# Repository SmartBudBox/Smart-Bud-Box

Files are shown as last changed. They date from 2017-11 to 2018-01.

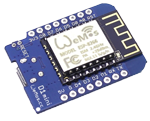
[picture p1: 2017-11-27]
Setup Tool/SBB Tool Source Code/Resources/WeMosV1.png

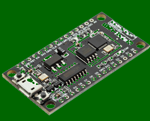
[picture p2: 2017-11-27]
Setup Tool/SBB Tool Source Code/Resources/WemosV2_activ.png

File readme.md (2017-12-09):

# Smart-Bud-Box
A small full automatic DIY Growbox with Web Interface for everyone.

# Install
Read the Manuals at /instrcutions/ for build the box and set up the Interface. We also got a little Growbook for the first steps

## Todo
- languages files for multilang
- ((write a growbook)) and put it to interface
- Addons like: libra, temp/humi for othside

## Wanna help?
You can help me by translate the language files (comming soon) into your langauge or make a new web design =)

## Short Video from the Interace with Planer
https://streamable.com/1owan

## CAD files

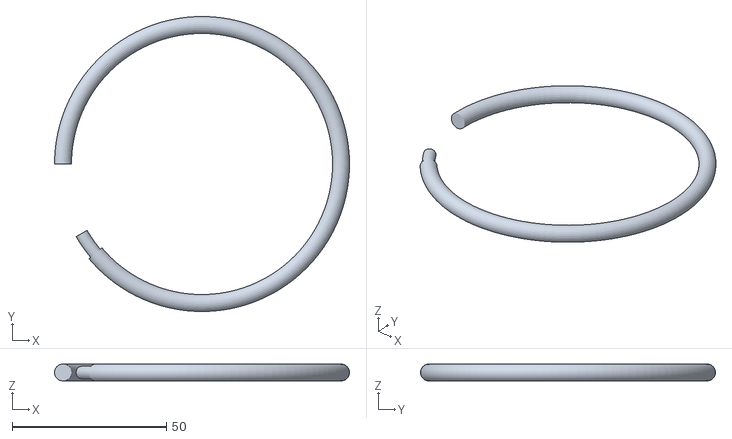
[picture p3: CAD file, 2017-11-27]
build_the_box/3d_printable_parts/water_ring_4mm_big.stl
95.5 x 95.5 x 5.48

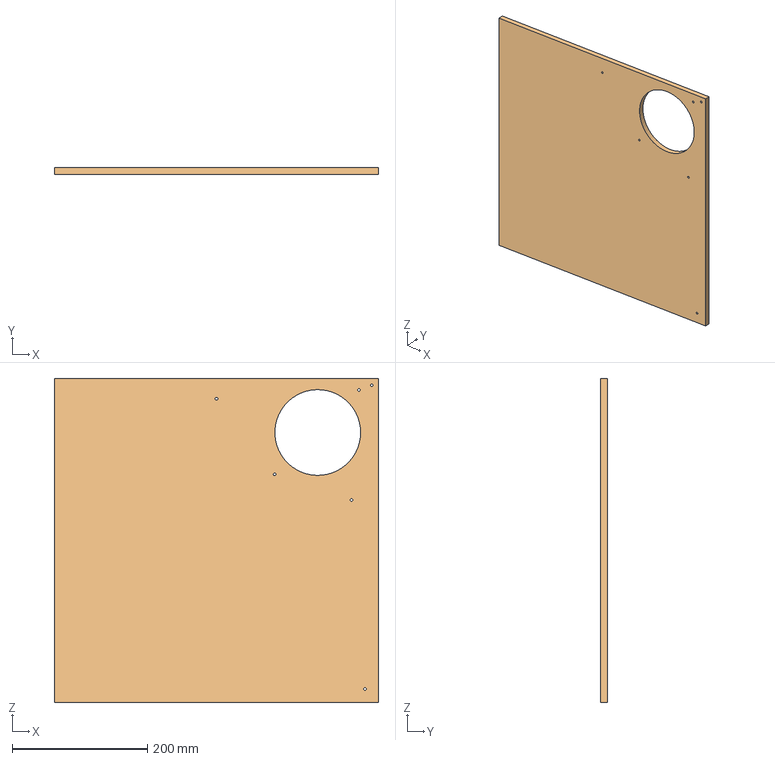
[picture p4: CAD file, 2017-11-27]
build_the_box/FreeCAD/FreeCAD_sbb.FCStd
480.0 x 10.0 x 480.0 mm

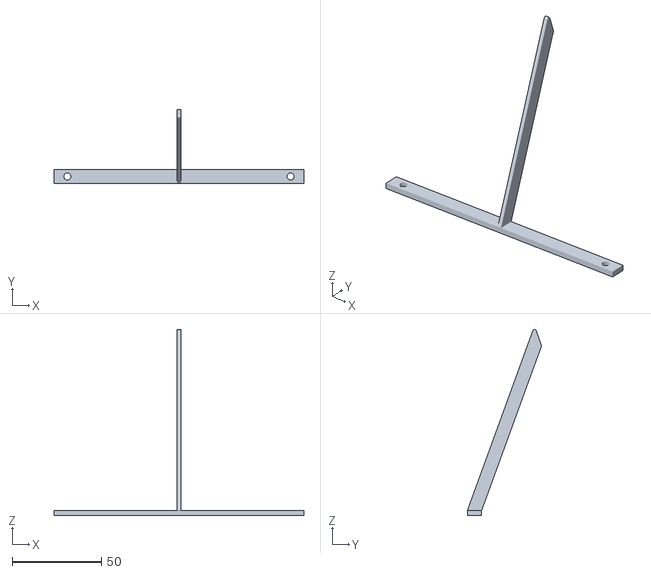
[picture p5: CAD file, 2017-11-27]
build_the_box/3d_printable_parts/140mm_fan_stand.stl
140.0 x 41.5 x 104.4

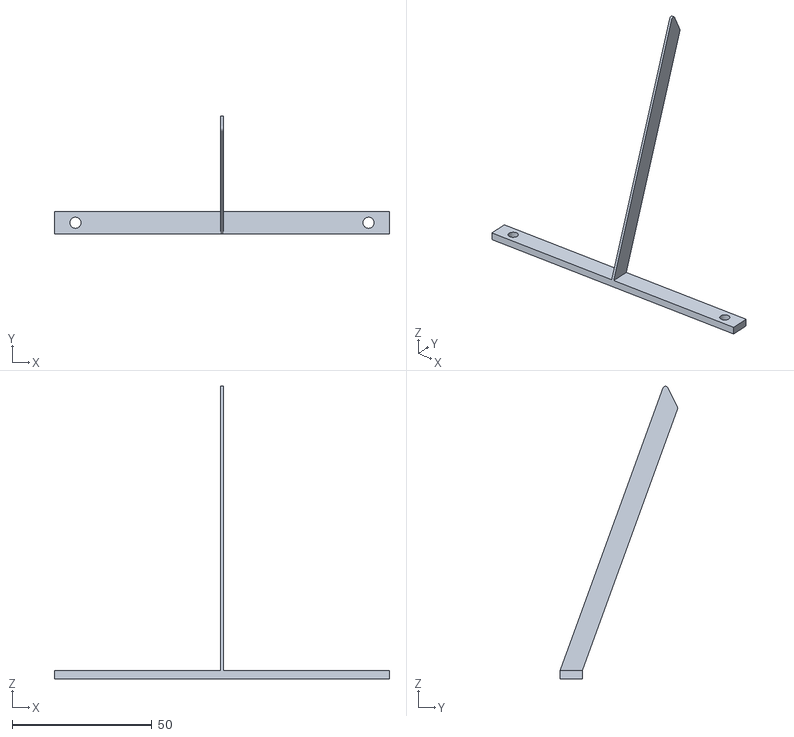
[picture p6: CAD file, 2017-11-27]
build_the_box/3d_printable_parts/120mm_fan_stand.stl
120.0 x 42.2 x 104.8

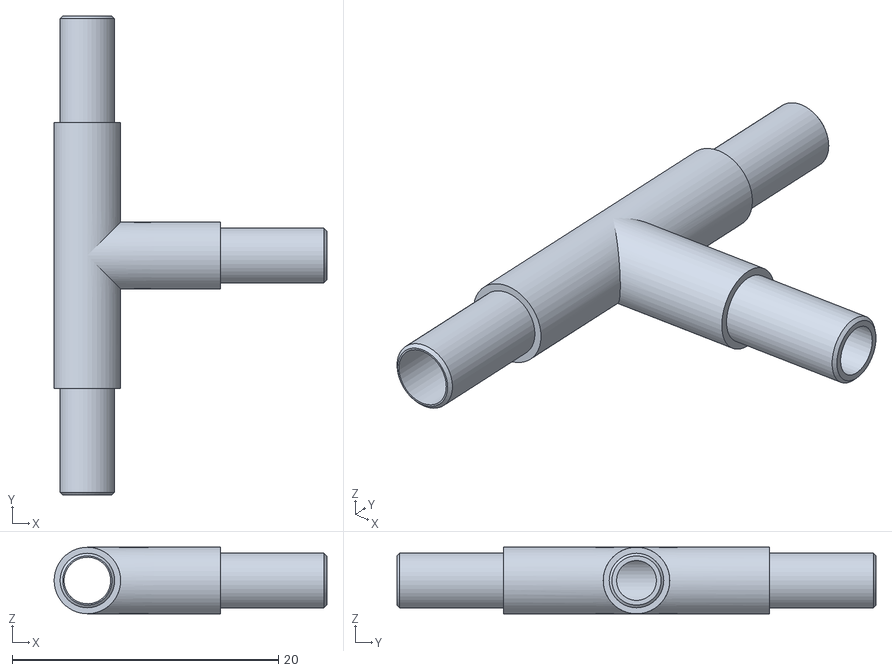
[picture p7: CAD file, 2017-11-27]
build_the_box/3d_printable_parts/t-hose.connector.stl
20.5 x 36.0 x 5.00

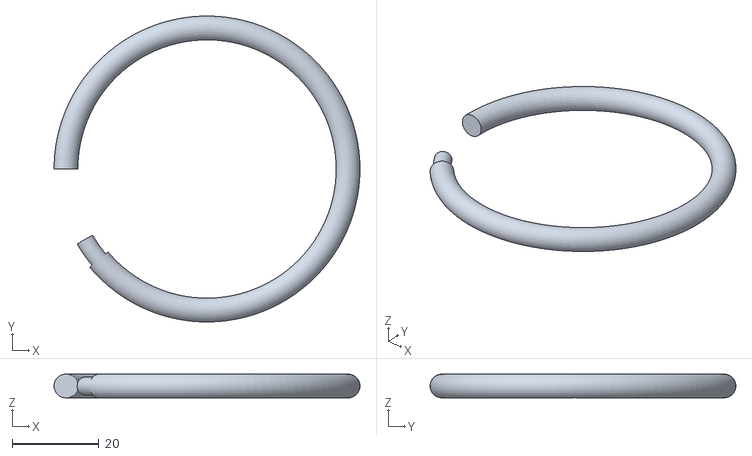
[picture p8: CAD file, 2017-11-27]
build_the_box/3d_printable_parts/water_ring_4mm_small.stl
70.5 x 70.5 x 5.48

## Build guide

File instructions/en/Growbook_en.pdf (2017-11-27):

# Preparation & Equipment

Selecting seeds
Buy feminised seeds from plants that don't get too big, indicas have an advantage. I can recommend www.Samenwahl.com as a source.

If you don't know what you want to plant, you can look for a certain variety in the seed database and sort by effect and many more: http://seedfinder.eu

Fertilizer | & | PH-Down
As a fertilizer I recommend you to add a mineral All-In-One fertilizer to the water: Hy-Pro Terra 500ml. Hy-Pro also has a liquid PH-down, you need a PH-down to lower the PH of your tap water (is 7) because the plant can only process the nutrients properly at 5.5-6PH. Rainwater would also be suitable as the PH value is lower from the house.

PH meter
Buy a PH meter to check your water for 10€ and you will get a good value (yellow meter).
Growing | and | potting | soil
You need two kinds of soils, one is a cultivating/herbal soil which is not so heavily fertilized for the beginning and the other one is potting soil for the further development. I recommend Compo Sana quality soil from the hardware store, you have a good price/performance ratio.

Jars
In order to preserve your harvest later on, you will need preserving jars, which are well sealed. I recommend 1-2 pieces with 1 litre capacity.
Flowerpot | with | saucer
Here, cheap plant pots with coasters from the DIY store are enough. It is important that the pot has holes at the bottom so that the water can get out. After all, water is always poured down to the bottom so that the fertiliser does not deposit. Get yourself three different sizes, a very small one for the cultivation (large diameter of your fist), a medium one (two fists diameter) and a big one (three fists diameter).
Ikea | 365+ | Reservoir | 2.3 | litres
We need the container as a water tank, if you have something similar at home and it fits into the box you can also take it. The advantage of the container is that you can make a mark at 2 liters. Then you only have to add water up to the mark Hy-Pro Terra (10ml) and adjust the pH value.

# Germination process

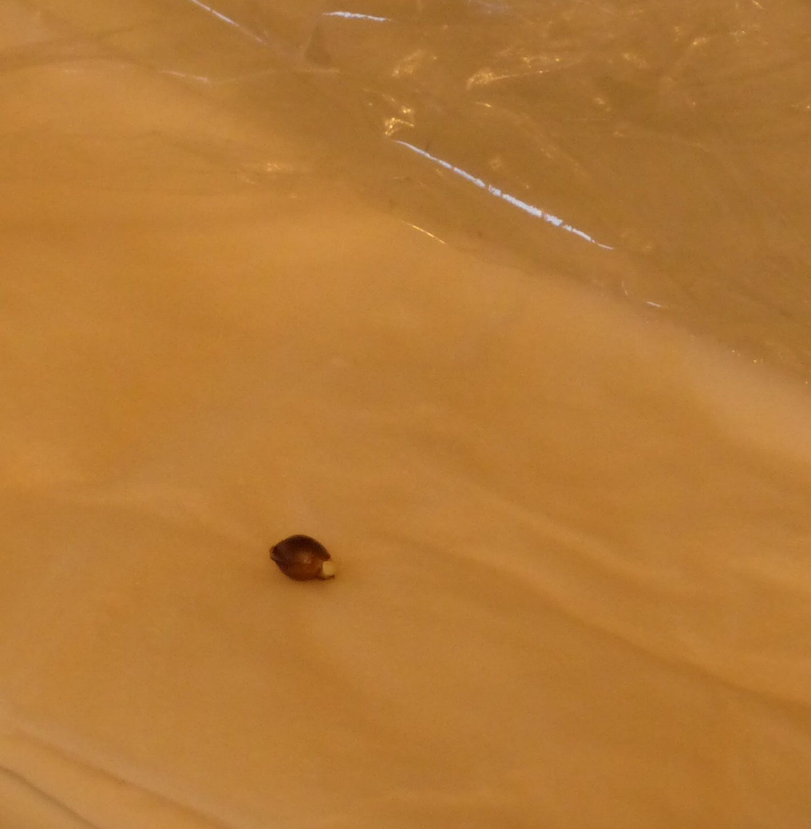
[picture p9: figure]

Duration: 2-6 days

For germination you need two small plates, two handkerchiefs, the seed and cling film. Now take a plate and put a handkerchief on it, moisten it well in front of it and then put the seed on it. The second handkerchief is also well moistened and put over it and a little bit pressed on. Then cover the whole thing with cling film so that the moisture cannot escape. Now you take the second plate and put it on top of it so there's no light coming in. Give the seed three days to germinate, then the rind opens and a small, fine root emerges.

# Pot seeds

If your seeds are germinated, you can take a small flower bowl and fill it with cultivated soil, fill the bowl with about 75 %. Then take the germinated seed with a pair of tweezers and place it in the middle with the root pointing downwards, then add one to two centimetres of soil and add it to the ground and water it well with normal water, preferably with a spoon or directly with the watering system.

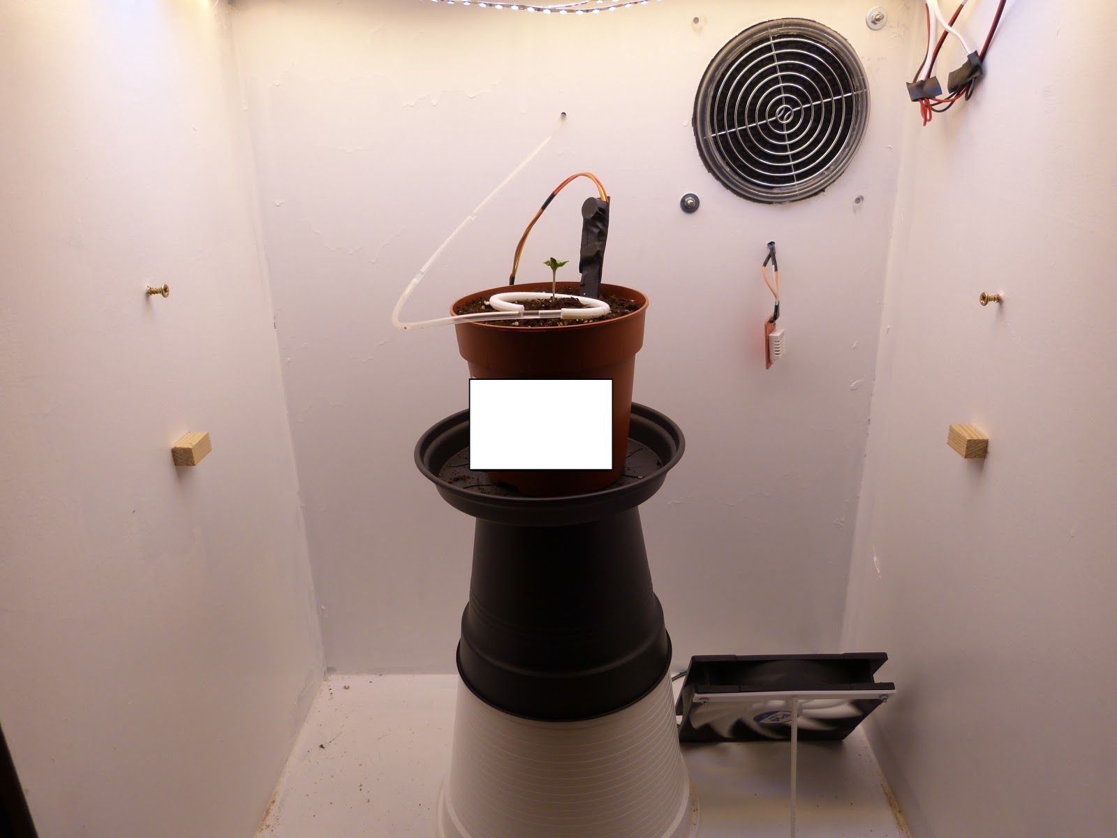
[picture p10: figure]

For the casting system, please proceed slowly,
e. g. with a casting time of 1000 milliseconds
and a waiting time of 200 seconds. The repetitions can be done at the beginning in two places depending on how big your pot is, your soil moisture reaches a value of about 500 the soil is wet and from 360-400 about the soil is dry again and you have to water again. You can see this best if the curve of the earth's moisture does not go down anymore but only
sideways.

Put the pot in the middle of the box, because the white lights are important for the vegetation phase, you can also put them underneath so that the plant is closer to the light. If you have installed a switch, you can turn off the warm white lights. With the lighting I advise you to have 20 hours of lighting and 4 hours rest I turn off my lights at 12 o' clock on and at 8 o' clock in the morning. You can now set the counter to the flower by clicking on it.

Now the seed can unfold and your plant can grow, make sure you don't water too much and stick to the sensor. Sometimes less is more.

# Growing season

Duration: approx. 2 weeks

The first vegetation phase is about 2 weeks, which means that the plant grows up. The best values are humidity at least 40% and the temperature at least 22 degrees Celsius. If you get too dry air, take a glass or bowl with a cloth in it and fill it with water, the cloth should stick out and put on the water.

At the beginning a plant grows quite fast and after two or three days you can fill up a little soil until the pot is completely filled.

Also, raise the pot a little higher at the beginning so that the plant gets enough light. If you take fruit flies, take a small glass of vodka glass, fill it with 50% water, 50% wine vinegar and a drop of water, then you have a good flytrap.

# Repot the plant

Duration: 7 days

Now look out of the pot and the first pair of leaves has formed (not the germination leaves) it is time to plant in the medium-sized pot and change the soil to the potting soil or add fertiliser via the water. If the soil is dry when repotting, it will be easier.

Take the medium-sized pot and fill it up to 30 % with the potting soil, then take the old pot and bend it a little bit on the sides so that you can get the plant out. Shake the soil around the plant as much as you can, but the plant does not exist. Now place the plant in your new pot and fill it with potting soil.

If the potting action is successful, you can water again and let your plant grow.

Don't be surprised if after potting the time takes longer until the soil would be dry (up to 7 days) this is normal as the roots dig in again and stretch out before the plant gets really thirsty again.

If the leaves should sink after repotting, it is quite normal that the roots need a little bit of time to cope with it.

# Topping

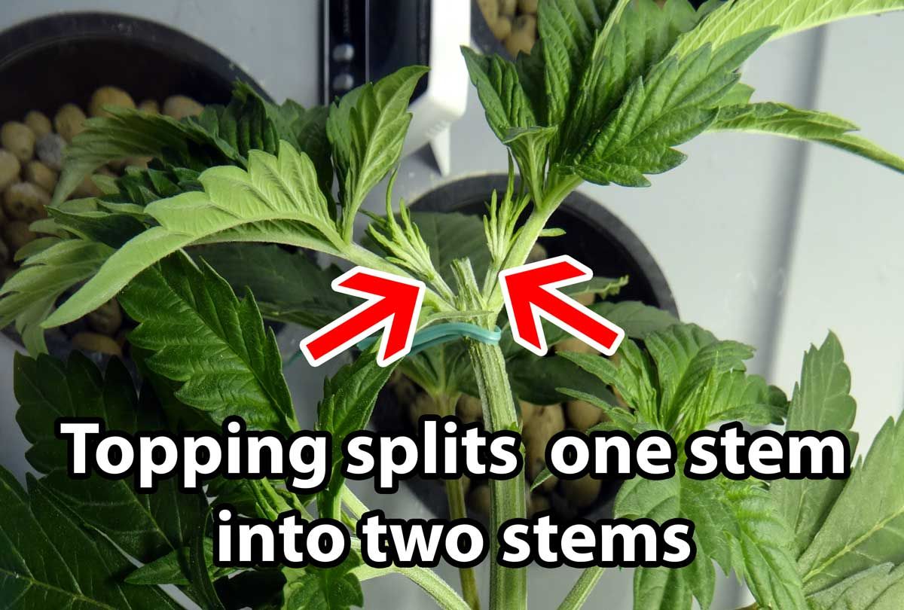
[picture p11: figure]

Duration: 3 days

If your plant already has the third pair of leaves and it still grows a little bit out in the middle, you can cut your plant there with a disinfected knife, scissors or something like that. Thus it does not grow up into the height anymore but forms several main drives which we can pass later on under the lattice. That increases your request considerably.

# Repot plant 2 & vegi 2

Duration: 2-5 weeks

Give your plant two to three days to recover after topping. Afterwards you can plant the pot in the middle pot on the big pot with potting soil.

Just follow the same procedure as for the first repot action. If your plant is too small from the height or grows rather bushy, you can repot it in such a way that just the root is planted in the ground and the stem sticks out more into the height. If not, repot the pot normally.

When your plant reaches the height of the lattice, place the lattice on top and let the stems grow through. As soon as the stem is through a grid, gently pull it down into the next grid hole. This way you can spread your main shoots in length.

# Blooming phase

Duration: 50-70 days

If the plant has grown well under the lattice, you can start flowering and the flowering can be initiated before. Depending on how much you want in Erne. Note also that in the flowering phase your plant grows again properly, so 50% of what it already is. It can be pulled through the grids, depending on how much space is available.

To start flowering with normal seeds (no automatics) you just have to change the lighting cycle to 12 hours of light 12 hours dark. The cold white light can now be switched off because the plant needs more warm white. It wouldn't matter if you added lighting, but it costs more electricity and the temperature in the box is higher.

The plant slowly gets hairs from which new shoots are formed and they should have a free path to the light, work a little bit with the lattice and pull down larger leaves. Around the flowers you will notice small white dots, the resin glands that become active and at the same time your plant will become thirsty. If you have poured in the vegi every 3-7 days it can happen that you now pour every 2 days.

About 2 weeks before harvesting you should leave off the fertilizer so that the plant can rinse all the minerals and you don't scratch later. Towards the end the leaves turn yellow, which is normal in autumn and the trees outside are no longer green.

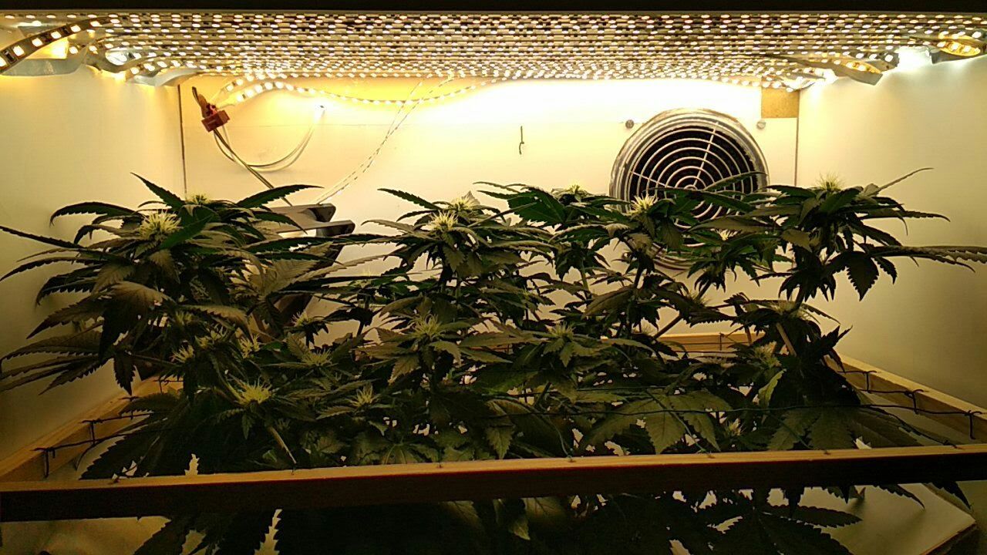
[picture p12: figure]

# Harvesting & Drying

Duration: 2 weeks

The flowering period lasts for about 2 months, 50-70 days depending on the variety. The information from the manufacturer is usually always very positive. You can also influence the effect of the harvest. Look at this graphic. Best you use a microscope eg for the PC, which are quite cheap to have.

Look at this when you harvest the soil is dry to get some moisture out of it. Before harvesting, it is advisable to turn off the light for 24 hours to send the plant to sleep.

When the day has come, you will
get some garden wire/string,
disposable gloves and a good pair
of scissors. Make sure that you stay undisturbed (nights) and that you have closed the room, the smell will be extreme. Cut off the sun sails (large blades) on the main propulsion. Then cut off the main drive at the bottom and thread it out of the grid, the more you do away from it, the better it goes.

If you have the main shoots removed, then cut the leaves off around the blossoms, if the small leaves remain on the blossom it is half as bad, there is enough resin on it that it is worthwhile to use them with.

Clears out the box and stretches the string across the Growroom on
the screws to the right and left of
the wall. Hang the shoots like on a

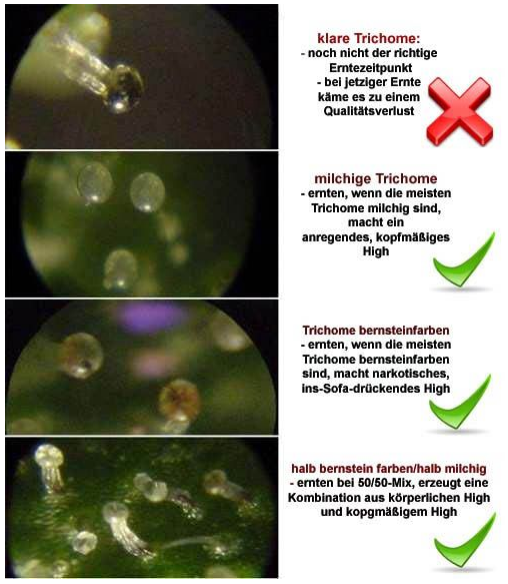
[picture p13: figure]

clothesline. Turns off the light of the box by pressing the green "Light" button.

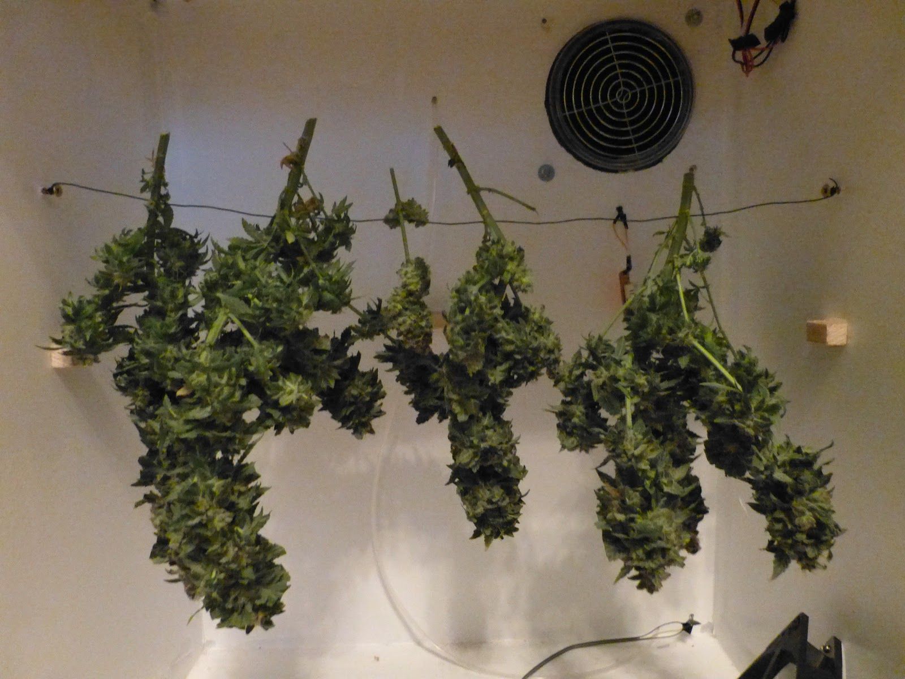
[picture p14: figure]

Now the 2 weeks are best left in the dark at 50% humidity until the main shoots break when bending. Then it's dry enough. Now you can cut the flowers from the main shoots or break them off as you like.

# Curing

Duration: min. 2 weeks

If you have the flowers then put them into the preserving jar, it is best if the jars are only half full. In the first 1-2 weeks you open the preserving jars daily so that the humidity can get out and it doesn't mildew.

After that you're finished, the curing process can be optimized and you can do up to two years, google it, then you can really refine the stuff and experience tastes you didn't know before.

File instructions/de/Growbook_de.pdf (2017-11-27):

# Vorbereitung & Equipment

Samen aussuchen
Kauft euch feminisierte Samen von Pflanzen die nicht all zu groß werden, indicas sind da im Vorteil. Als Quelle kann ich www.Samenwahl.com empfehlen.

Wenn ihr nicht wisst was ihr anpflanzen wollt könnt ihr bei der Samendatenbank erst einmal nach einer gewissen Sorte Ausschau halten und dabei nach Wirkung und vielen weiteren sortieren: http://seedfinder.eu

Dünger | & | PH-Down
Als Dünger empfehle ich euch einen mineralischen All-In-One Dünger den ihr mit in das Wasser gebt: Hy-Pro Terra 500ml. Von Hy-Pro gibt es auch einen flüssigen PH-Down, einen PH-Down braucht ihr um den PH Wert eures Leitungswassers zu senken (liegt bei 7), denn die Pflanze kann nur bei 5,5-6PH die Nährstoffe sauber verarbeiten. Regenwasser würde sich auch eignen da dort der PH Wert von haus aus niedriger ist.

PH Messgerät
Kauft euch für 10€ ein PH Messgerät mit dem ihr euer Wasser überprüfen könnt, sonei günstiges reicht (gelbes Gerät).
Anzucht | und | Blumenerde
Ihr braucht zwei Arten von Erden, einmal eine Anzucht / Kräutererde die nicht so stark gedüngt ist für den Anfang und danach Blumenerde für den weiteren Verlauf. Ich empfehle Compo Sana Qualitätserde aus dem Baumarkt, da habt ihr ein gutes Preis/Leistungsverhältnis.

Einmachgläser
Um später eure Ernte auf zu bewahren braucht ihr Einmachgläser, die sind gut dicht. Ich empfehle 1-2 Stück mit 1 Liter Rauminhalt.
Blumentopf | mit | Untersetzer
Hier reichen so günstige Pflanzenbecher mit Untersetzer aus dem Baumarkt. Wichtig ist dass der Topf unten Löcher hat das dort das Wasser raus kann. Denn gegossen wird immer so viel bis unten Wasser raus kommt damit sich der Dünger nicht ablagern kann. Besorgt euch drei verschiedene Größen, ein ganz kleinen für die Anzucht (Faustgroßer Durchmesser), einen mittleren (zwei Fäuste Durchmesser) und einen großen (drei Fäuste Durchmesser).
Ikea | 365+ | Vorratsbehälter | 2,3 | Liter
Den Behälter benötigen wir als Wassertank, wenn ihr so was ähnliches daheim habt und es in die Box passt könnt ihr das auch nehmen. Der Vorteil bei dem Behälter ist dass man sich bei 2 Liter eine Markierung machen kann. Dann muss man nur bis zur Markierung Wasser rein, eine Verschlusskappe Hy-Pro Terra (10ml) rein und den PH Wert anpassen.

# Keimung

Dauer: 2-6 Tage

Für die Keimung braucht ihr zwei kleine Teller zwei Taschentücher, den Samen und Frischhaltefolie. Nehmt nun ein Teller und legt dort ein Taschentuch drauf, macht es davor gut feucht und legt danach den Samen darauf. Das zweite Taschentuch wird ebenfalls gut feucht gemacht und drüber gelegt und ein bisschen angedrückt. Danach das Ganze mit Frischhaltefolie überziehen damit die Feuchtigkeit
nicht entweichen kann. Jetzt nehmt ihr den zweiten
Tellern und leg den oben drauf damit kein Licht
reinkommt. Gib dem Samen ruhig drei Tage Zeit bis dieser keimen kann, dann öffnet sich die Schale und es dringt eine kleine feine Wurzel heraus.

# Samen eintopfen


Ist eurer Samen gekeimt könnt ihr ein kleine Blumenschale nehmen und diese mit Anzuchterde füllen, füllt die Schale mit ca 75 %. Danach nehmt ihr am besten mit einer Pinzette den gekeimten Samen und legt ihn in die Mitte rein mit der Wurzel nach unten, danach noch ein bis zwei cm Erde drauf und das ganze erstmal gut angießen mit normalen Wasser, am besten mit einem Löffel oder direkt mit dem Gießsystem.

Bei dem die Gießsystem geht bitte langsam vor z.b. mit einer Gießzeit von 1000 Millisekunden und einer Wartezeit von 200 Sekunden. Die Wiederholungen könnt ihr am Anfang auf zwei Stellen je nachdem wie
groß euer Topf ist, erreicht eure Erdfeuchte
ein Wert von ca. 500 ist die Erde nass und
ab 360-400 ungefähr ist die Erde wieder trocken und ihr müsst wieder gießen. Das erkennt ihr am besten daran wenn die Kurve


der Erdfeuchte nicht mehr runter geht sondern nur noch seitwärts.

Stellt den Topf am besten in die Mitte der Box da dort die weißen Lichter sind die für die Vegetationsphase wichtig sind, ihr könnt auch etwas drunter Stellen damit die Pflanze näher am Licht ist. Falls ihr einen Schalter verbaut habt dann könnt ihr die warmweißen Lichter ausschalten. Bei der Beleuchtung rate ich euch zu 20 Stunden Beleuchtung und 4 Stunden Ruhezeit ich schalte mein Licht um 12 Uhr an und um 8 Uhr morgens aus. Den Zähler könnt ihr nun auf die Blüte stellen mit einem Klick darauf.

Jetzt kann der Samen sich entfalten und eure Pflanze kann wachsen, achtet darauf dass ihr nicht zu viel gießen tut und haltet euch an den Sensor. Manchmal ist weniger mehr.

# Vegetationsphase

Dauer: ca. 2 Wochen

Die erste Vegetationsphase geht ca 2 Wochen, sie die dazu dass die Pflanze erstmal groß wird. Die besten Werte dazu sind Luftfeuchtigkeit mindestens 40% und die Temperatur mindestens auf 22 Grad. Falls ihr eine zu trockene Luft bekommt ein Glas oder eine Schale mit einem Tuch darin nehmen und mit Wasser befüllen, das Tuch sollte herausragen und das Wasser anziehen.

Am Anfang wächst eine Pflanze ziemlich schnell und ihr könnt nach zwei oder drei Tagen schon ein bisschen Erde nachschütten so lange bis der Topf komplett gefüllt ist.

Stellt den Topf auch ein wenig höher am Anfang damit die Pflanze genug Licht bekommt. Wenn ihr Fruchtfliegen war nimmt, nehmt ein kleines Glas (Wodkaglas), füllt es 50% mit Wasser, 50% mit Weinessig und einen tropfen Spüli, dann habt ihr eine gute Fliegenfalle.

# Pflanze umtopfen

Dauer: 7 Tage

Schaut eure Pflanze nun gut aus dem Topf und das erste Blattpaar hat sich gebildet (nicht die Keimungsblätter) wird es Zeit in den mittelgroßen Topf um zu pflanzen und die Erde auf die Blumenerde zu wechseln bzw über das Wasser Dünger zuzuführen. Schaut das beim umtopfen die Erde trocken ist, dann geht es einfacher.

Nimm den mittelgroßen Topf und füllt ihn zu 30 % mit der Blumenerde auf, danach nehmt ihr den alten Topf knickt ihn an den Seiten ein wenig ein so dass ihr die Pflanze raus bekommt. Schüttelt um die Pflanze die Erde so gut es geht ab aber besteht nicht die Pflanze. Nun legt ihr die Pflanze in eurer neuen Topf rein und füllt diese mit Blumenerde auf.

Ist die Umtopfaktion geglückt könnt ihr erstmal wieder gießen und eure Pflanze wachsen lassen.

Wundert euch nicht wenn nach dem umtopfen die Zeit länger dauert bis die Erde würde trocken ist (bis zu 7 Tage) das ist normal da die Wurzeln sich erstmal wieder eingraben und ausstrecken bevor die Pflanze wieder richtig durstig wird.

Wenn sich die Blätter senken sollten nach dem Umtopfen ist das ganz normal die Wurzeln brauchen ein bisschen bis sie wieder klar kommen.

# Topping


Dauer: 3 Tage

Hat eure Pflanze schon das dritte Blattpaar und es wächst in der Mitte noch ein wenig raus könnt ihr dort eure Pflanze mit einem desinfizierten Messer, Schere oder sowas in der Art abschneiden. Dadurch wächst sie nicht mehr in die Höhe sondern bildet mehrere Haupttriebe die wir später unterm Gitter hindurch führen können. Das steigert euren Antrag erheblich.

# Pflanze umtopfen 2 & Vegi 2

Dauer: 2-5 Wochen

Gibt eure Pflanze nach dem Topping zwei bis drei Tage Zeit sich zu erholen. Danach könnt ihr von dem mittleren Topf auf den großen Topf umpflanzen wieder mit Blumenerde.

Geht einfach wieder so vor wie bei der ersten umtopf Aktion. Sollte eure Pflanze von der Höhe her zu klein sein oder eher buschig wachsen könnt ihr die so umtopfen dass gerade die Wurzel in die Erde steckt und der Stiel mehr in die Höhe ragt. Anderenfalls ganz normal wieder umtopfen.

Erreicht eure Pflanze die Höhe vom Gitter, dann legt das Gitter drauf und lasst die Stängel durch wachsen. Sobald der Stängel durch ein Gitter ist, zieht ihn vorsichtig runter in das nächste Gitterloch. So könnt ihr eure Haupttriebe schön in die Länge spreizen.

# Blütephase

Dauer: 50-70 Tage

Ist die Pflanze schon schön unterm Gitter gewachsen könnt ihr die Blüte einleiten, die Blüte kann auch schon zuvor eingeleitet werden. Je nach dem wie viel ihr an Erne wollt. Beachtet auch dass in der Blütephase eure Pflanze nochmals ordentlich wächst, so 50% von dem was sie schon ist. Dabei kann sie weiterhin durch die Gitter gezogen werden, je nachdem wieviel Platz noch vorhanden ist.

Um Die Blütephase einzuleiten bei normalen Samen (keine Automatics) müsst ihr einfach den Beleuchtungszyklus ändern auf 12 Stunden Licht 12 Stunden dunkel. Das Kaltweiße Licht kann jetzt abgeschaltet werden, da die Pflanze nun mehr Warmweiss braucht. Zwar würde es nichts ausmachen zusätzlich zu beleuchten, aber das kostet mehr Strom und die Temperatur in der Box ist höher.

Die Pflanze bekommt langsam Härchen aus denen sich neue Triebe bilden und die sollten möglichst freie Bahn haben zum Licht, arbeitet ein bisschen mit dem Gitter und zieht größere Blätter runter. Um die Blüten herum werdet ihr kleine weiße Punkte wahrnehmen, das sind die Harzdrüsen die aktiv werden, gleichzeitig wird eure Pflanze auch durstiger. Habt ihr in der Vegi noch alle 3-7 tage einmal gegossen kann es vorkommen dass ihr jetzt alle 2 Tage gießt.

Ca. 2 Wochen bevor ihr erntet solltet ihr den Dünger weg lassen damit die Pflanze die ganzen Mineralien ausspülen kann und ihr später kein Kratzen habt. Gegen Ende werden die Blätter gelb, das ist normal im Herbst sind die Bäume draußen auch nicht mehr grün.

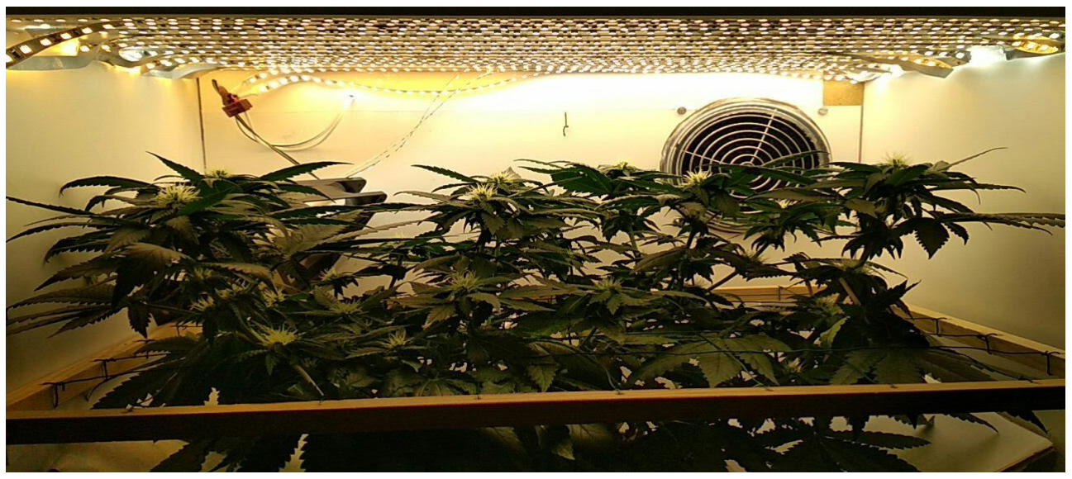
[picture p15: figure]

# Ernte & Trocknung

Dauer: 2 Wochen

Die Blütephase geht ca. 2 Monate lang so 50-70 Tage je nach Sorte. Die Angaben vom Hersteller sind meist immer sehr positiv. Durch die Ernte könnt ihr auch nochmal die Wirkung beeinflussen. Schau dabei auf diese Grafik. Am besten ihr verwendet ein Mikroskop zB für den PC, die sind recht günstig zu haben.

Schaut das wenn ihr Erntet die Erde trocken ist um so schonmal Feuchtigkeit raus zu bekommen. Bevor man erntet sollte man auch 24 Stunden lang das Licht ausschalten um die Pflanze in den Schlaf zu schicken.

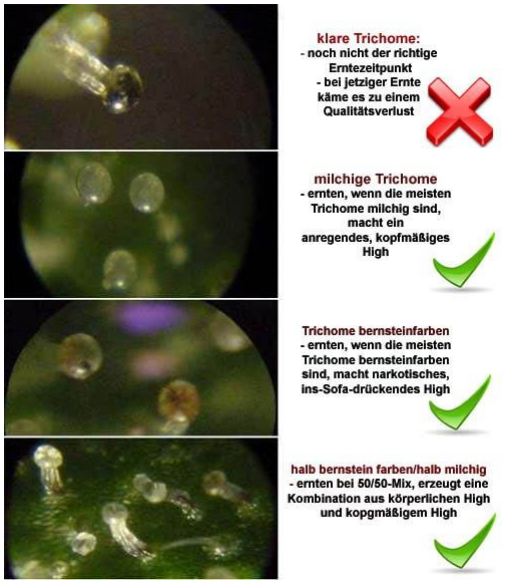
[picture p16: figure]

Ist der Tag gekommen dann legt
euch Gartendraht/schnur,
Einweghandschuhe und eine gute Schere zu. Achtet dass ihr ungestört bleibt (Nachts) und das ihr den Raum geschlossen habt, der Geruch wird extrem. Trennt dann die Sonnensegel (große Blätter) am Haupttrieb ab. Danach den Haupttrieb unten abschneiden und aus dem Gitter fädeln, umso mehr ihr davor weg macht umso besser geht es auch raus.

Habt ihr die Haupttriebe weg, dann schneidet um die Blüten die Blätter noch weg, wenn die kleinen Blätter an der Blüte dran bleiben ist das halb so schlimm, da ist genug Harz dran das es sich lohnt diese mit zu verwerten.

Räumt die Box aus und spannt die Schnur quer durch den Growroom an den Schrauben rechts und links der Wand. Hängt da die
Triebe auf wie auf einer Wäscheleine.
Schaltet das Licht der Box aus, dazu auf
den grünen “Licht” Button drücken.


Jetzt bleiben die 2 Wochen am besten bei 50% Luftfeuchte im dunklem hängen, bis sich die Haupttriebe beim biegen brechen. Dann ist es trocken genug. Jetzt könnt ihr die Blüten von den Haupttrieben abschneiden bzw abbrechen, wie ihr wollt.

# Aushärten

Dauer: min. 2 Wochen

Habt ihr die Blüten dann ab damit in das Einmachglas, am besten ist es wenn die Gläser nur zur Hälfte gefüllt sind. In den ersten 1-2 Wochen öffnet ihr die Einmachgläser täglich damit die Luftfeuchte raus kann und es nicht schimmelt.

Danach ist seit ihr eigentlich schon fertig, das Aushärten kann man noch optimieren und bis zu zwei JAhre betreiben, am besten mal googeln, dann könnt ihr das Zeug richtig veredeln und werdet Geschmäcke erleben die ihr nicht kanntet.

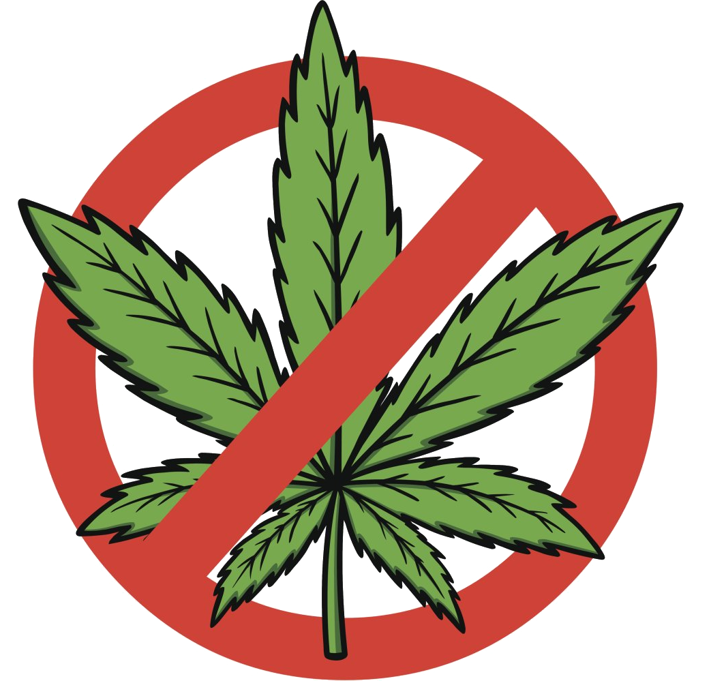
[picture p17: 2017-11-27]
Setup Tool/SBB Tool Source Code/Resources/Close.png

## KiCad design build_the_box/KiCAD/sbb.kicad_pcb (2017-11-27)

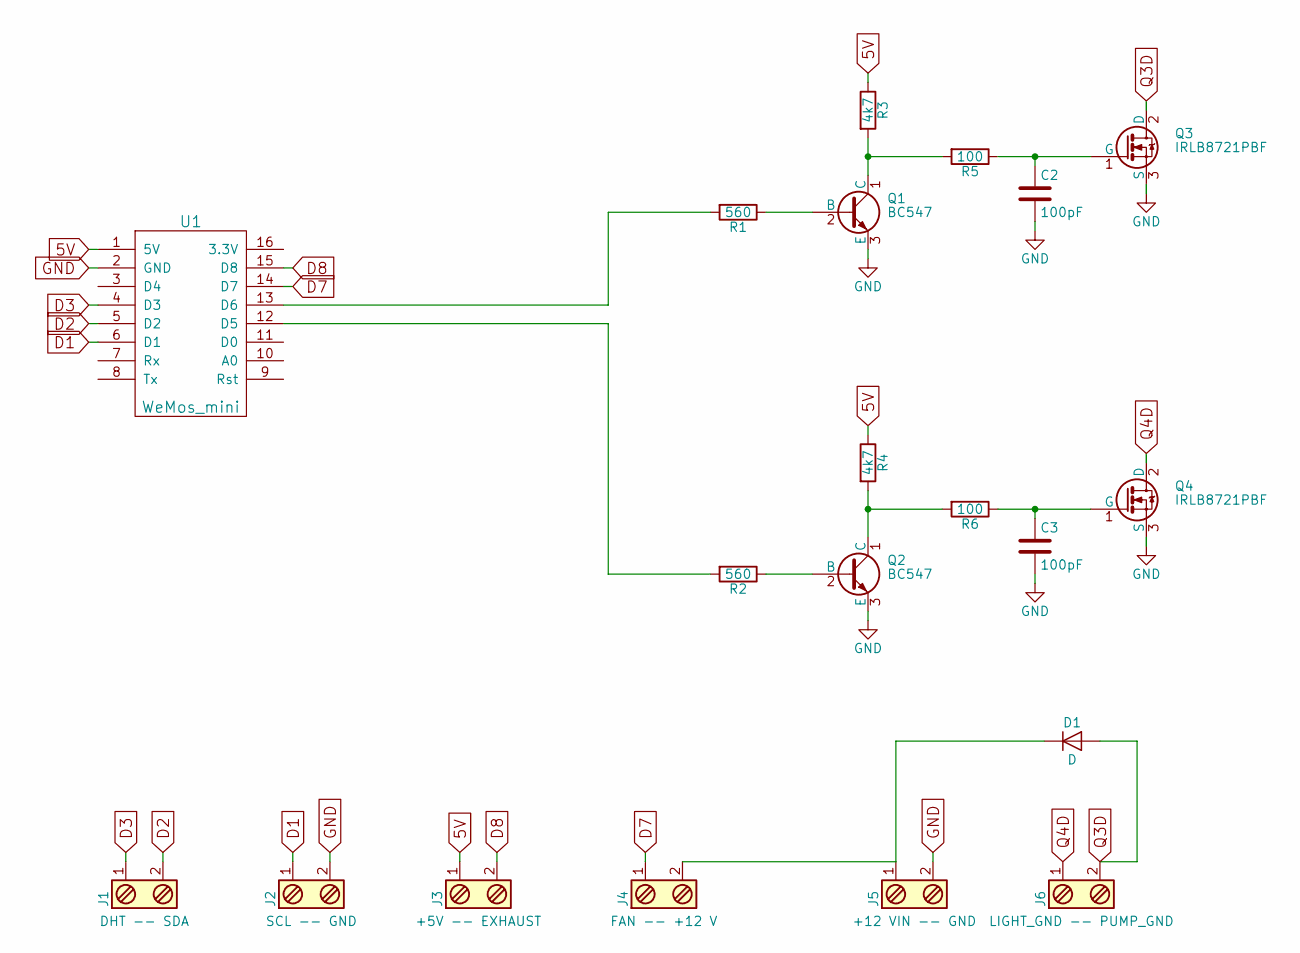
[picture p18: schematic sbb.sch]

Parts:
C2, C3: 100pF; C_Disc_D3.0mm_W2.0mm_P2.50mm
D1: D; D_5W_P10.16mm_Horizontal
J1: DHT -- SDA; TerminalBlock_Pheonix_MKDS1.5-2pol
J2: SCL -- GND; TerminalBlock_Pheonix_MKDS1.5-2pol
J3: +5V -- EXHAUST; TerminalBlock_Pheonix_MKDS1.5-2pol
J4: FAN -- +12 V; TerminalBlock_Pheonix_MKDS1.5-2pol
J5: +12 VIN -- GND; TerminalBlock_Pheonix_MKDS1.5-2pol
J6: LIGHT_GND -- PUMP_GND; TerminalBlock_Pheonix_MKDS1.5-2pol
Q1, Q2: BC547; TO-92_Molded_Narrow
Q3, Q4: IRLB8721PBF; TO-220_Vertical
R1, R2: 560; R_Axial_DIN0207_L6.3mm_D2.5mm_P10.16mm_Horizontal
R3, R4: 4k7; R_Axial_DIN0207_L6.3mm_D2.5mm_P10.16mm_Horizontal
R5, R6: 100; R_Axial_DIN0207_L6.3mm_D2.5mm_P10.16mm_Horizontal
U1: WeMos_mini; wemos_d1_mini

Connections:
5V: J3.1, R3.1, R4.1, U1.1 (5V)
D1: J2.1, U1.6 (D1)
D2: J1.2, U1.5 (D2)
D3: J1.1, U1.4 (D3)
D7: J4.1, U1.14 (D7)
D8: J3.2, U1.15 (D8)
GND: C2.2, C3.2, J2.2, J5.2, Q1.3 (E), Q2.3 (E), Q3.3 (S), Q4.3 (S), U1.2 (GND)
unnamed: C2.1, Q3.1 (G), R5.1
unnamed: C3.1, Q4.1 (G), R6.1
unnamed: D1.1 (K), J4.2, J5.1
unnamed: Q1.1 (C), R3.2, R5.2
unnamed: Q1.2 (B), R1.1
unnamed: Q2.1 (C), R4.2, R6.2
unnamed: Q2.2 (B), R2.1
unnamed: R1.2, U1.13 (D6)
unnamed: R2.2, U1.12 (D5)
Q3D: D1.2 (A), J6.2, Q3.2 (D)
Q4D: J6.1, Q4.2 (D)

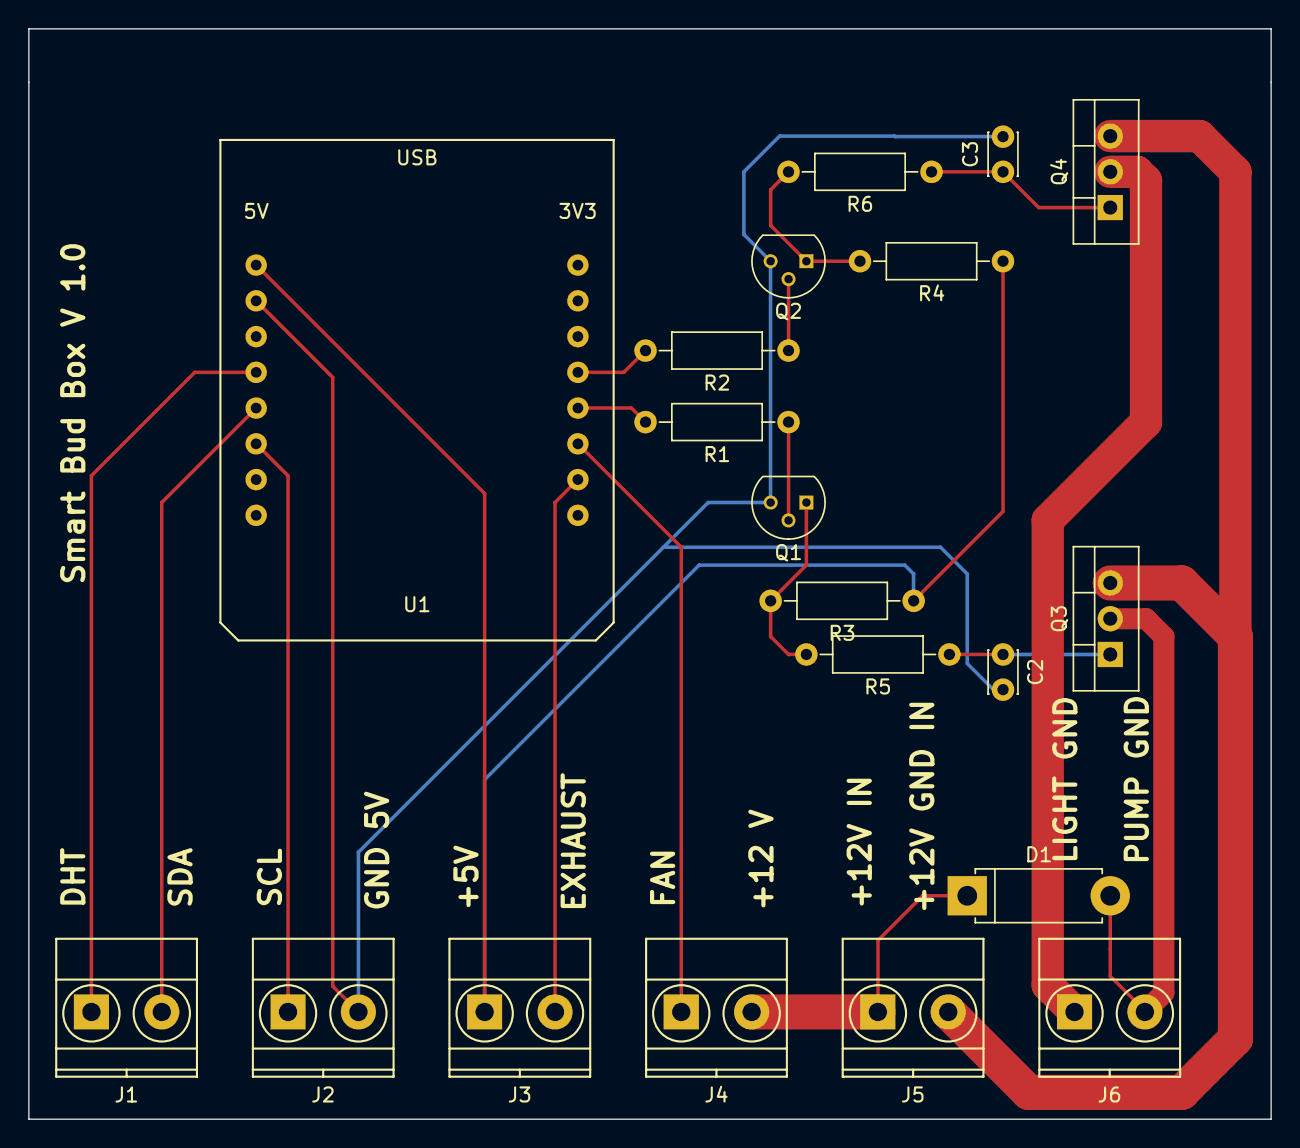
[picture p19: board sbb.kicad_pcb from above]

Board: 2 copper layers, 88.3 x 77.5 mm, 20 parts (0 on the bottom side), 18 nets.

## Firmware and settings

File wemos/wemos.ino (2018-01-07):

/*
   SETUP HERE


   wemos pinout: https://wiki.wemos.cc/products:d1:d1_mini
   wemos driver https://wiki.wemos.cc/downloads

   install wemos board to ide: https://learn.sparkfun.com/tutorials/esp8266-thing-hookup-guide/installing-the-esp8266-arduino-addon

   install the 
   DHT Sensor Libary
   ArduinoJSon
   Adafruit Unified Sensor
   
    from "Sktech - Include Libary - Manage Libarys"

*/
const char* ssid = "wlan"; // name of your wlan ssid
const char* pass = "password";    // wlan wpa password or key for wep
const char* host = "site.com"; // hostname, ip adresses wont work, example: host.com
const int httpPort = 80;
const char* host_url = ""; // folder without slash at end, example: /your/folder or blank for main dir
const char* api_password = "123456"; // password for interface wich defined at config.inc.php
const long sensor_submission_interval = 10000; // interval for sensor data submission in ms: 60000 for 60 secound
/*
   SETUP END


   setup finished, do not change any thing here if u dont know what u are doing
*/



#include "ESP8266WiFi.h"
#include <Wire.h>
#include <DHT.h>
#include <ArduinoJson.h>




#define FAN 13      // D7
#define EXHAUST 15  // D8
#define PUMPE 14    // D5
#define LICHT 12    // D6
#define DHT_1 0     // D3
#define SOIL_SCL D1  // D1
#define SOIL_SDA D2  // D2

DHT dht1(DHT_1, DHT22);

int status_light = 0;
int status_fan = 1024;
int status_exhaust = 1024;
String website_data = "";
unsigned long sensor_submission_last = 0;


void setup()
{
  analogWriteFreq(31300);
  
  Serial.begin(115200);
  Wire.begin();
  writeI2CRegister8bit(0x20, 6);
  delay(100);
  dht1.begin();

  
  pinMode(BUILTIN_LED, OUTPUT);  // initialize onboard LED as output
  pinMode(LICHT, OUTPUT);
  pinMode(PUMPE, OUTPUT);
  digitalWrite(LICHT, HIGH);
  digitalWrite(PUMPE, HIGH);

  // give soil sensor time to switch into sensor mode
  int i = 0;
  while(i < 10){ 
    writeI2CRegister8bit(0x20, 3);
    readI2CRegister16bit(0x20, 4);
    i++;
    delay(100);
  }
  digitalWrite(BUILTIN_LED, HIGH);

  Serial.println("connecting to wifi ap");

  WiFi.mode(WIFI_STA);
  WiFi.begin(ssid, pass);

  while (WiFi.status() != WL_CONNECTED) {
    delay(500);
    Serial.print(".");
  }
  Serial.println("");
  Serial.println("wifi connected");

  read_website_data("clear_transmissions");
}

void writeI2CRegister8bit(int addr, int value) {
  Wire.beginTransmission(addr);
  Wire.write(value);
  Wire.endTransmission();
}

unsigned int readI2CRegister16bit(int addr, int reg) {
  Wire.beginTransmission(addr);
  Wire.write(reg);
  Wire.endTransmission();
  delay(20);
  Wire.requestFrom(addr, 2);
  unsigned int t = Wire.read() << 8;
  t = t | Wire.read();
  return t;
}

/**
   in url u give the action parameters and other get parameters, like: submit&value=1
   index.php?page... will be done automatically
*/

void read_website_data(String url)
{
  website_data = "";
  url =  String(host_url) + "/index.php?page=wemos&action=" + String(url);
  Serial.print("connecting to ");
  Serial.println(host);

  // Use WiFiClient class to create TCP connections
  WiFiClient client;
  if (!client.connect(host, httpPort)) {
    Serial.println("connection failed");
    return;
  }

  // We now create a URI for the request
  url = url + "&box=" + String(ESP.getChipId()) + "&password=" + api_password;

  Serial.print("requesting adress: ");
  Serial.println(host + url);

  // This will send the request to the server
  client.print(String("GET ") + url + " HTTP/1.1\r\n" +
               "Host: " + host + "\r\n" +
               "Connection: close\r\n\r\n");
  unsigned long timeout = millis();
  while (client.available() == 0) {
    if (millis() - timeout > 10000) {
      Serial.println(">>> Client Timeout !");
      client.stop();
      return;
    }
  }
  // Read all the lines of the reply from server and print them to Serial

  int x = 0;
  while (client.available()) {
    String line = client.readStringUntil('\r');
    
    line.trim();

    if (line.startsWith("{")) {
      website_data += line;
    }

    x++;
    
  }

  Serial.print("parsed content: ");
  Serial.println(website_data);

  delay(300);

  return;
}

void loop()
{

  // read sensordata and submit to api action: sensordata if interval reached
  unsigned long currentMillis = millis();
  if (currentMillis - sensor_submission_last >= sensor_submission_interval) {
      digitalWrite(BUILTIN_LED, LOW);
      delay(500);
      digitalWrite(BUILTIN_LED, HIGH);
    int soil = readI2CRegister16bit(0x20, 0);    
    read_website_data("sensordata&temp=" + String(dht1.readTemperature()) + "&humi=" + String(dht1.readHumidity()) + "&soil=" + soil);
    sensor_submission_last = currentMillis;
  }


  // submit current status
  read_website_data("boxstatus&light=" + String(status_light) + "&fan=" + String(status_fan) + "&exhaust=" + String(status_exhaust));

  // read new jobs
  read_website_data("read_transmission_json");
  StaticJsonBuffer<200> jsonBuffer;
  JsonObject& root = jsonBuffer.parseObject(website_data);

  if (!root.success())
  {
    Serial.println("parseObject() failed");
    return;
  }

  const char* command = "";
  const char* value = "";

  command   = root["command"];
  value     = root["value"];

  if (strcmp (command, "switch_light") == 0)
  {
    status_light = atoi(value);

    Serial.print("switching light from ");
    Serial.print(status_light);
    Serial.print(" to ");
    Serial.println(value);

    if (status_light == 1)
    {
      digitalWrite(LICHT, LOW);
    }
    else
    {
      digitalWrite(LICHT, HIGH);
    }

  }

  if (strcmp (command, "set_exhaust") == 0)
  {
    status_exhaust = atoi(value);

    Serial.print("set exhaust from ");
    Serial.print(status_exhaust);
    Serial.print(" to ");
    Serial.println(value);


    analogWrite(EXHAUST, status_exhaust);
  }

  if (strcmp (command, "set_fan") == 0)
  {
    status_fan = atoi(value);

    Serial.print("set fan from ");
    Serial.print(status_fan);
    Serial.print(" to ");
    Serial.println(value);


    analogWrite(FAN, status_fan);
  }

  if (strcmp (command, "watering") == 0)
  {
    int runtime = atoi(value);

    Serial.print("watering with pump runtime of ");
    Serial.println(runtime);

    if (status_light == 1)
    {
      digitalWrite(LICHT, HIGH);
    }

    delay(500);
    digitalWrite(PUMPE, LOW);
    delay(runtime);
    digitalWrite(PUMPE, HIGH);
    delay(500);

    if (status_light == 1)
    {
      digitalWrite(LICHT, LOW);
    }
  }

  delay(100);
}

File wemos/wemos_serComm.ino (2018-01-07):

/*
   SETUP HERE
   wemos pinout: https://wiki.wemos.cc/products:d1:d1_mini
   wemos driver https://wiki.wemos.cc/downloads
   install wemos board to ide: https://learn.sparkfun.com/tutorials/esp8266-thing-hookup-guide/installing-the-esp8266-arduino-addon
   install the
   DHT Sensor Libary
   ArduinoJSon
   Adafruit Unified Sensor

    from "Sktech - Include Libary - Manage Libarys"
*/
//const long sensor_submission_interval = 10000; // interval for sensor data submission in ms: 60000 for 60 secound








//*********************************************************************************
//Hier sind die Credentials die vom Setup Tool kommen                *
//*********************************************************************************
String ssid;                         //Speicherplatz beginnt bei 10  Lï¿½nge Speicherplatz 1
String pass;                         //Speicherplatz beginnt bei 40  Lï¿½nge Speicherplatz 2
String host;                         //Speicherplatz beginnt bei 70  Lï¿½nge Speicherplatz 3
String httpPort;                     //Speicherplatz beginnt bei 100  Lï¿½nge Speicherplatz 4
String host_url;                     //Speicherplatz beginnt bei 107  Lï¿½nge Speicherplatz 5
String api_password;                 //Speicherplatz beginnt bei 137 Lï¿½nge Speicherplatz 6
String sensor_submission_interval;   //Speicherplatz beginnt bei 167 Lï¿½nge Speicherplatz 7
String incoming;                     //EmpfÃ¤nger Variable fÃ¼r Serielle Schnittstelle
int CredentialsOK;
////Hat so la la Funktioniert ----------------------------------------------
char incomingBytes[80]; // = 0;
int lf = 13;
////Hat so la la Funktioniert ----------------------------------------------
//*********************************************************************************

/*
   SETUP END
   setup finished, do not change any thing here if u dont know what u are doing
*/

//************************************************************************
//Hier ist der INCLUDE BEREICH                                           *
//************************************************************************
#include "ESP8266WiFi.h"  //WIFI Board                                   *
#include <Wire.h>                                                        *
#include <DHT.h>          //Feuchte Sensoren                             *
#include <ArduinoJson.h>  //Libary für die Sensoren                      *
#include <EEPROM.h>       //Schreiben und Lesen aus / in EEPROM          *
//************************************************************************


//************************************************************************
//Hier ist der Definde BEREICH                                           *
//************************************************************************
#define FAN 13      // D7
#define EXHAUST 15  // D8
#define PUMPE 14    // D5
#define LICHT 12    // D6
#define DHT_1 0     // D3
#define SOIL_SCL D1  // D1
#define SOIL_SDA D2  // D2
//************************************************************************

DHT dht1(DHT_1, DHT22);


int status_light = 0;
int status_fan = 1024;
int status_exhaust = 1024;
String website_data = "";
unsigned long sensor_submission_last = 0;



//************************************************************************
// start reading from the first byte (address 0) of the EEPROM
//************************************************************************
byte value;
//************************************************************************


int inByte;
char inText[300];
int index2;


void setup()
{
  analogWriteFreq(31300);

  Wire.begin();

  Serial.begin(115200);
  Serial.println("SBB Controller gestartet");
  EEPROM.begin(512);

  pinMode(BUILTIN_LED, OUTPUT);  // initialize onboard LED as output
  pinMode(LICHT, OUTPUT);
  pinMode(PUMPE, OUTPUT);
  digitalWrite(LICHT, HIGH);
  digitalWrite(PUMPE, HIGH);
  

  // give soil sensor time to switch into sensor mode
  int i = 0;
  while (i < 10) {
    writeI2CRegister8bit(0x20, 3);
    readI2CRegister16bit(0x20, 4);
    i++;
    delay(100);
  }

  writeI2CRegister8bit(0x20, 6);
  delay(100);
  
  
  dht1.begin();
  
  //************************************************************************
  //Laden der Credentials mit 20 Sekunden WarteZeit
  //Falls die Credentials über das Setup geändert werden sollen
  //************************************************************************
  memset(incomingBytes, 0, sizeof(incomingBytes));
  Serial.println("Warte auf Credentials Change");
  int counter = 0;
  for (int counter = 0; counter < (20); ++counter)
  {

    if (Serial.available() > 0) {

      // read the incoming byte:
      //incomingByte = Serial.read();
      Serial.readBytesUntil(lf, incomingBytes, 80);

      // say what you received in ASCII
      //Serial.print("I received: ");
      Serial.println(incomingBytes);
      CheckData(incomingBytes);
      memset(incomingBytes, 0, sizeof(incomingBytes));

    }
    delay(1000);
  }
  //************************************************************************
  CredentialsOK = 0;
  sensor_submission_interval = GETsensor_submission_interval();


  //
  ////WIEDER LÖSCHEN ODER DEAKTIVIEREN
  //ClearEEPROM();                 //*

  memset(incomingBytes, 0, sizeof(incomingBytes));
  //--------------------------------
  while (CredentialsOK != 1)
  {
    delay(500);
    //Serial.println("Warte auf Daten");
    //Serial.println(CredentialsOK);


    //Hat so la la Funktioniert ----------------------------------------------
    if (Serial.available() > 0) {

      // read the incoming byte:
      //incomingByte = Serial.read();
      Serial.readBytesUntil(lf, incomingBytes, 80);

      // say what you received in ASCII
      //Serial.print("I received: ");
      Serial.println(incomingBytes);
      CheckData(incomingBytes);
      memset(incomingBytes, 0, sizeof(incomingBytes));

    }
    //Hat so la la Funktioniert ----------------------------------------------



  }


  ssid = GETssid();
  pass = GETpass();
  host = GEThost();
  httpPort = GEThttpPort();
  host_url = GEThost_url();
  api_password = GETapi_password();
  sensor_submission_interval = GETsensor_submission_interval();



  digitalWrite(BUILTIN_LED, HIGH);
  Serial.println("connecting to wifi ap");

  WiFi.mode(WIFI_STA);
  WiFi.begin(ssid.c_str(), pass.c_str());

  while (WiFi.status() != WL_CONNECTED) {
    delay(500);
    Serial.print(".");
  }
  Serial.println("");
  Serial.println("wifi connected");

  read_website_data("clear_transmissions");
}

void writeI2CRegister8bit(int addr, int value) {
  Wire.beginTransmission(addr);
  Wire.write(value);
  Wire.endTransmission();
}

unsigned int readI2CRegister16bit(int addr, int reg) {
  Wire.beginTransmission(addr);
  Wire.write(reg);
  Wire.endTransmission();
  delay(20);
  Wire.requestFrom(addr, 2);
  unsigned int t = Wire.read() << 8;
  t = t | Wire.read();
  return t;
}
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
